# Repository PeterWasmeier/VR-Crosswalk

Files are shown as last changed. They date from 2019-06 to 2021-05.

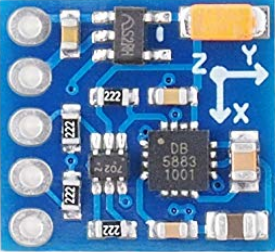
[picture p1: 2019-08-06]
Mini/Documents/Triple Axis Compass - GY271/GY271.png

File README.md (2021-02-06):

# VR-Crosswalk
Documents, Source code, wiring and 3D files of the omnidirectional treadmill "VR-Crosswalk"

About the subfolders:

- "Introduction"
Contains documents, describing the "VR-Treadmill" in general. If you don't know what it this repository about, first read the documents inside this folder.

- "Algorithms"
There you will find some documents, describing the math behind this treadmill.

- "Mini"
This "Mini" version is just a proof of concept, it's not suitable for humans, can't take weights and is just for your desk to play with. 

- "Light"
The "Light" version is a real omnidirectional treadmill for humans, but not able to handle stairs and elevators. Walking, sitting and driving a car is possible.

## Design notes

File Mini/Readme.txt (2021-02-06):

In this folder, there are all 3D files, wiring and source code of the "VR-Crosswalk-Mini".

This "Mini" version is just a proof of concept, it's not suitable for humans, can't take weights and is just for your desk to play with. 

The "Mini" version is also not able to handle stairs, elevator or cars, just: testing the formulars and a proof of concept. Maximum shoe length is 160mm or "22" (EU shoe size).

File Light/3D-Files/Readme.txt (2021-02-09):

This folder contains 3D files for the "VR-Crosswalk-Light". These files are created with "Autodesk Fusion 360".

Here are two subfolders:

- "general"
Here you will find 3D files of items that you can buy on Amazon, Ebay, and so on. These parts are needed by the "VR-Crosswalk-Light".

- "special"
The 3D parts inside this folder are special for the "VR-Crosswalk-Light". You can't buy them, you have to create them by your own.

- "Fusion360"
This is a backup what is currently in development. This is the whole machine with all parts and screws. Will be updated around once a week.

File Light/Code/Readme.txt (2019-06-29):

The source-code is made for the hardware: "Arduino Uno".

You have to use the IDE "Arduino Genuino V1.8.9" in order to open this project. 

You can download the IDE here:

http://www.arduino.cc/

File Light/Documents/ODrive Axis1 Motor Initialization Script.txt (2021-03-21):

odrv0.axis1.motor.config.pole_pairs=7
odrv0.axis1.controller.config.input_mode=INPUT_MODE_TRAP_TRAJ
odrv0.axis1.motor.config.motor_type = MOTOR_TYPE_HIGH_CURRENT
odrv0.axis1.motor.config.current_lim=25
odrv0.axis1.controller.config.vel_limit=20
odrv0.axis1.motor.config.calibration_current=2
odrv0.axis1.motor.config.torque_constant=0.0147678571428571
odrv0.axis1.motor.config.pre_calibrated = False
odrv0.axis1.encoder.config.use_index=False
odrv0.axis1.encoder.config.pre_calibrated=False
odrv0.save_configuration()
odrv0.reboot ()

odrv0.axis1.encoder.config.bandwidth = 3000
odrv0.axis1.encoder.config.mode = ENCODER_MODE_INCREMENTAL
odrv0.axis1.encoder.config.cpr=8192
odrv0.save_configuration()
odrv0.reboot ()

odrv0.axis1.requested_state = AXIS_STATE_FULL_CALIBRATION_SEQUENCE
dump_errors(odrv0)

odrv0.axis1.motor.config.pre_calibrated=True
odrv0.axis1.trap_traj.config.vel_limit = 0.5
odrv0.axis1.trap_traj.config.accel_limit = 140
odrv0.axis1.trap_traj.config.decel_limit = 140
odrv0.axis1.controller.config.inertia = 0
odrv0.axis1.controller.config.input_mode=INPUT_MODE_TRAP_TRAJ
odrv0.save_configuration()
odrv0.reboot ()

odrv0.axis1.encoder.config.use_index=True
odrv0.axis1.requested_state = AXIS_STATE_ENCODER_INDEX_SEARCH
odrv0.axis1.encoder.config.pre_calibrated=True
odrv0.save_configuration()
odrv0.axis1.encoder.is_ready
odrv0.reboot ()

odrv0.axis1.controller.config.pos_gain=56
odrv0.axis1.controller.config.vel_gain=0.053
odrv0.axis1.controller.config.vel_integrator_gain=0.05
odrv0.axis1.min_endstop.config.gpio_num=8
odrv0.axis1.min_endstop.config.debounce_ms=1
odrv0.axis1.min_endstop.config.is_active_high=True
odrv0.axis1.min_endstop.config.enabled=True
odrv0.save_configuration()
odrv0.reboot ()

odrv0.axis1.min_endstop.endstop_state
dump_errors(odrv0,True)

odrv0.axis1.requested_state = AXIS_STATE_ENCODER_INDEX_SEARCH
odrv0.axis1.encoder.is_ready
dump_errors(odrv0,True)

odrv0.axis1.requested_state = AXIS_STATE_CLOSED_LOOP_CONTROL
odrv0.axis1.controller.input_pos=
odrv0.axis1.requested_state = AXIS_STATE_IDLE

odrv0.axis1.controller.config.vel_ramp_rate=0.5
odrv0.axis1.min_endstop.config.offset=2
odrv0.axis1.controller.config.homing_speed=-0.5
odrv0.axis1.requested_state=AXIS_STATE_HOMING

AXIS_ERROR_HOMING_WITOUT_ENDSTOP
**********************************************************
Tuning

odrv0.axis1.controller.config.pos_gain=20
odrv0.axis1.controller.config.vel_gain=0.04
odrv0.axis1.controller.config.vel_integrator_gain=0

odrv0.axis1.requested_state = AXIS_STATE_CLOSED_LOOP_CONTROL
odrv0.axis1.controller.input_pos=
odrv0.axis1.requested_state = AXIS_STATE_IDLE
dump_errors(odrv0,True)

odrv0.axis1.requested_state = AXIS_STATE_ENCODER_INDEX_SEARCH
odrv0.axis1.encoder.is_ready
dump_errors(odrv0,True)

start_liveplotter(lambda:[odrv0.axis1.encoder.pos_estimate, odrv0.axis1.controller.pos_setpoint])

start_liveplotter(lambda:[odrv0.axis1.motor.current_control.Iq_setpoint,odrv0.axis1.motor.current_control.Iq_measured])

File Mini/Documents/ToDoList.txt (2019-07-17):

Some Notes from Peter Wasmeier for stuff to improve

- den Arduino anders herum platzieren (180° gedreht) da sonst der USB Anschluß nicht genutzt werden kann (Motor im Weg!)
* die 4er Löcher in den unteren Trittplatten müssen 0,1mm größer werden
-die 3mm Löcher in der Platine müssen auch wirklich 3mm haben sonst lässt sich die Platine nicht mit der PCB Grundplatte verschrauben
*es muss ein Kabelloch für den Encoder rein
-die PCB Platte doch mit 4mm dicke? Weil es wakelt zu viel, oder aber eine Unterlegscheibe unter den SK8. Vorher aber prüfen ob die Lötpunkte unter der Trittplattenplatine ausreichend sind um den Millimeter zu überbrücken zwischen Alu-Trittplatte und Base.
*die 5er Schraubenlöcher der SK Teile kleiner, damit dort ein Gewinde rein kann
*das Loch für die Stepper um 0,1mm größer machen
- prüfen ob der kleine Servo mehr als nur 180° beherrscht, sonst lassen sich die Beine nicht kreuzen
- die Formeln der Platte auf vier Quadranten verteilen

Legende:
- noch zu tun
* bereits erledigt

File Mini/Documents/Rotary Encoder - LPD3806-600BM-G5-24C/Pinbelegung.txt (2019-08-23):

Die Belegung der Anschlüsse ist:
- sw(black) GND, 
- rt(red) VCC, 
- ws(white) PIN A, 
- gn(green) PIN B.
PIN A und PIN B sind Open Collector Ausgänge, also PullUp.Widerstände nicht vergessen zu programmieren.

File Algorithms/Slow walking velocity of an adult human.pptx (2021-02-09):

## Slow walking velocity of an adult human

The slow, normal walking speed of an adult human is around 3,5km/h.

α=atan((35cm)/(15cm))×180/π= 66,8°

Slow walking speed | 3,5km/h
Step length at 3,5km/h around | 70cm
Steps per hour (with 70cm) | 5000
Time to take a single step (70cm) | 0,72s
Feet distance while standing | 30cm

In other words
To take one full step (70cm) in 0,72s, the axis
has to rotate from 0° to +66,8°.
This makes around 92,8° per second or 15,5rpm
where the disc has to spin.

Note: 15,5rpm is not the fastest speed which has to be
achieved, because the rotation speed depends on
tangens and the feet distance (while standing).

70cm

35

α

-20

-10

10

20

-35

30cm

## Walking straight ahead with 70cm in 0,72s

Note: as you can see, the highest rpm is about 30rpm or 180°/second.

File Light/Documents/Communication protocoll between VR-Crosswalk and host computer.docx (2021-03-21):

# VR-Crosswalk

## Communication protocol between VR-Crosswalk and host computer.

The device VR-Crosswalk can tell the host computer where the foots of the operator are located, in which angle each foot is currently orientated and the current state of the device.

The communication between VR-Crosswalk and the host computer is using Bluetooth. The communication speed is 38400 baud, 8 data bits. There is no need to select stop-bit or parity, it doesn’t matter. The host must look for the Bluetooth device “VR-Crosswalk”, connect to it and the Bluetooth connection can be handled as a normal COM port (RS232). The PIN, to connect to the device, is by default: 1234

Once the connection is established, and the host is listening on the COM port, the device will send its current state, each foot location and orientation by itself as soon as a foot has moved.

The host computer can also ask the device to move any axis. But in this case, it is forbitten for the operator to use the device. If host send a move command, but an operator is detected by the device, the command is rejected. For safety reason, each axis movement will be performed in very slow speed.

The communication between host and VR-Crosswalk is done by using 6 bytes data packages. Every data package is 6 bytes long. There are up to looks like this:

1.Byte | 2.Byte | 3.Byte | 4.Byte | 5.Byte | 6.Byte
Message ID | Value #1 (8 Bits) | Value #2 (8 Bits) | Value #3 (8 Bits) | Value #4 (8 Bits) | Checksum
Message ID | Value #1 (16 Bits, signed INT) | | Value #2 (16 Bits, signed int) | | Checksum
Message ID | Value #1 (32 Bits, signed long) | | | | Checksum
Message ID | Value #1 (32 bits as float) | | | | Checksum

The checksum is an XOR operation of the first five bytes.

Commands from host to VR-Crosswalk

Rotate device

This command, send by host, will rotate the VR-Crosswalk by the given value in units. This movement is relative. So, if you want to rotate the device by 200 units from the current position, set for Value #1 the number 200.

1.Byte | 2.Byte | 3.Byte | 4.Byte | 5.Byte | 6.Byte
Message ID | Value #1 (32 Bits as signed long) | | | | Checksum
0x10 | any positive or negative number | | | | Checksum

### Current state

The current state is sent from VR-Crosswalk to the host computer every 0,1 seconds. The state is four bytes long. Its value is defined as:

Byte | 1 | | | | | | | | 2 | | | | | | | | 3 | | | | | | | | 4
Bit | 7 | 6 | 5 | 4 | 3 | 2 | 1 | 0 | 7 | 6 | 5 | 4 | 3 | 2 | 1 | 0 | 7 | 6 | 5 | 4 | 3 | 2 | 1 | 0 | CRC
| 0 | 0 | 0 | 0 | 0 | 0 | 0 | 0

- Byte 2, Bit 7:

### Left Foot location, X-Coordinate

Byte | 1 | | | | | | | | 2 | 3 | 4
Bit | 7 | 6 | 5 | 4 | 3 | 2 | 1 | 0 | Lowbyte | Highbyte | CRC
| 0 | 0 | 0 | 0 | 0 | 0 | 0 | 1 | X-Coordinate in 0,1mm | X-Coordinate in 0,1mm

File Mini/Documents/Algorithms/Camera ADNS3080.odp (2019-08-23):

## Virtual Reality Treadmill "Crosswalk"

## Thema: Trittplatten die den Füßen folgen

## Virtual Reality Treadmill "Crosswalk"

## Vorwort

In diesem Dokument geht es darum, wie das Gerät den Füßen des Menschen folgen kann.

Hierfür werden Sensoren und Aktoren benötigt und die notwendigen Formeln hergeleitet.

## Aufbau von “Crosswalk”

## die Plattform kann sich um sich selbst drehen

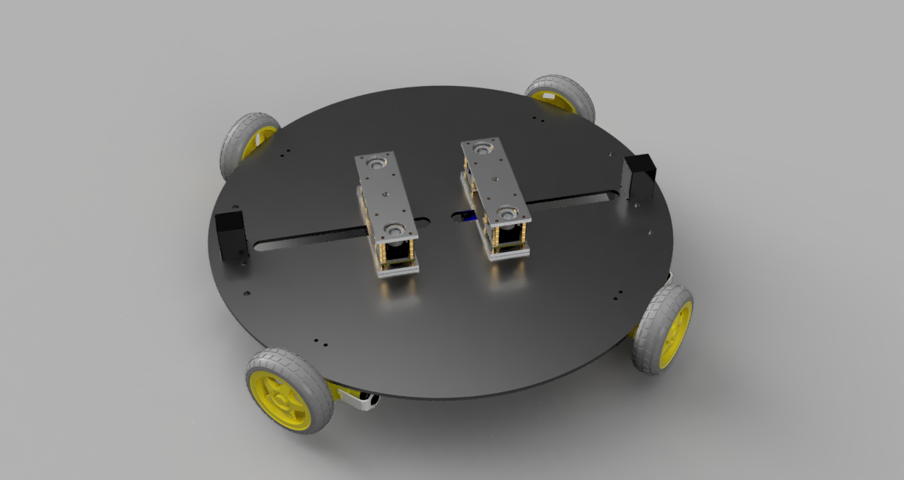
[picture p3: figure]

1. Trittplatte

2. Trittplatte

d

2 Motoren für

die horizontale

Ausrichtung

der Trittplatten.

Plattform

4 Motoren

## die horizontale Achse Ansicht von unten

## die Trittplatten sind mit einem Zahnriemen verbunden

Drehen sich diese Motoren,
ändert sich der Abstand der
Trittplatten.

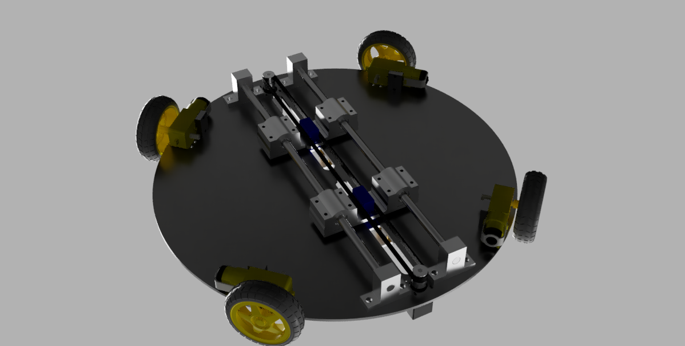
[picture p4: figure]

d

## eine Trittplatte für jeden Fuß

## auf einer Trittplatten sind Sensoren anzuordnen

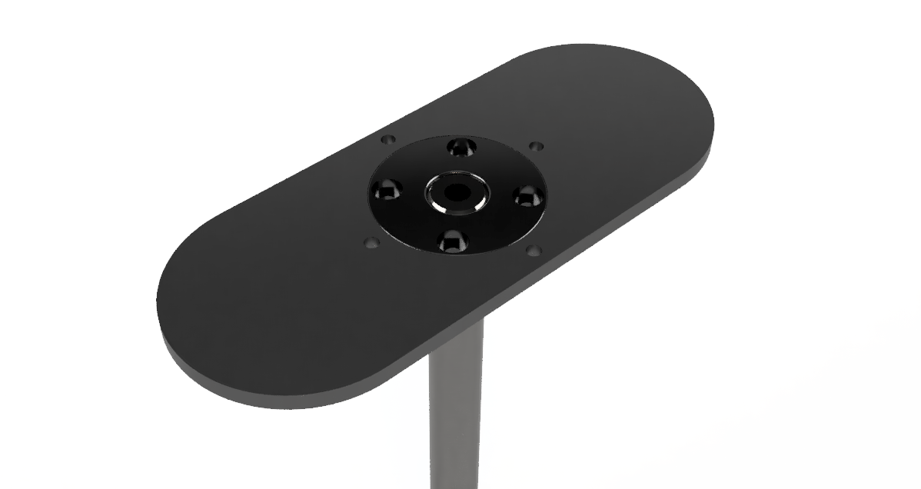
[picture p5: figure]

## geeignete Sensoren

## ADNS3080

Bei dem ADNS3080 handelt es sich um einen

Sensor wie er in vielen Computermäusen

eingebaut ist.

Dieser erfasst die X- und Y- Bewegungsrichtung

gegenüber einer Oberfläche.

Wenn dieser Sensor auf der Trittplatte befestigt wird, wird er die Bewegungsrichtung des Fußes gegenüber der stillstehenden Trittplatte erfassen.

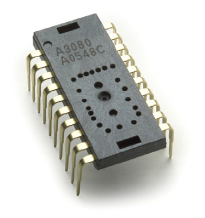
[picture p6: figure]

## geeignete Sensoren

## ADNS3080

Diesen Sensor gibt es

auch mit einer Linse.

Diese Linse ermöglicht es dem Sensor

zusätzlich in die Tiefe zu “sehen”.

Mit 15,-€ ist dieser Sensor recht günstig.

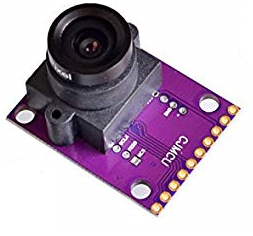
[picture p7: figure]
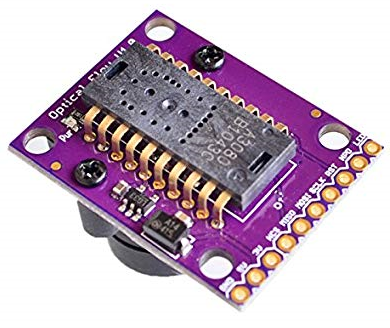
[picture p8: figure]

## Positionierung der Sensoren

## die Trittplatte kann sich drehen

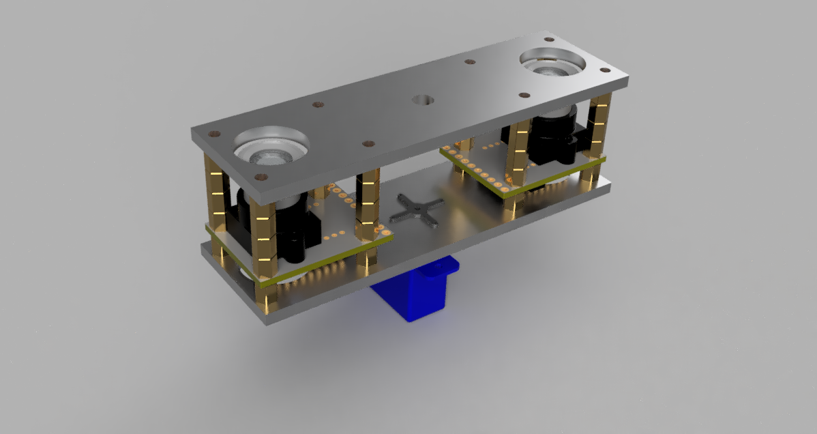
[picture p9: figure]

erster ADNS3080

Trittplatte

zweiter ADNS3080

Hinweis:
die Sensoren sind um 180°

gegeneinander verdreht.

Servo:

dreht die Trittplatte

## Mögliche Fußbewegungen

## vor/zurück, links/rechts und um sich selbst drehen

d

## ∆x und ∆y Daten vom ADNS3080

## beide ADNS3080 liefern delta-Werte

Jeder Sensor liefert

delta-Werte für

x und y sobald eine

Bewegung erkannt

wird.

Wichtig: die delta-
Werte sind senkrecht
zum Sensor.

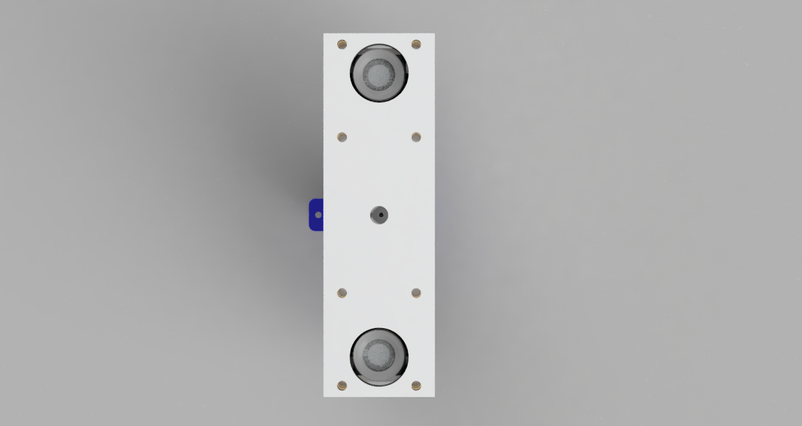
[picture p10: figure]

∆x₁

∆y₁

Bei m handelt es sich

um den konstanten
Abstand der Sensoren.

∆y₂ und ∆x₂ sind deshalb
negativ, da die Kamera
auf dem Kopf steht.

m

-∆y₂

-∆x₂

## ein Fuß wird bewegt 1. neue Position im Raum

## die Koordinaten von x₁ / y₁ und x₂ / y₂ ändern sich

∆x₁

∆y₁

-∆x₂

-∆y₂

(x₂ / y₂)

(x₁ / y₁)

(x'₁ / y'₁)

(x'₂ / y'₂)

x'₁=x₁+∆x₁

y'₁=y₁+∆y₁

x'₂=x₂-∆x₂

y'₂=y₂-∆y₂

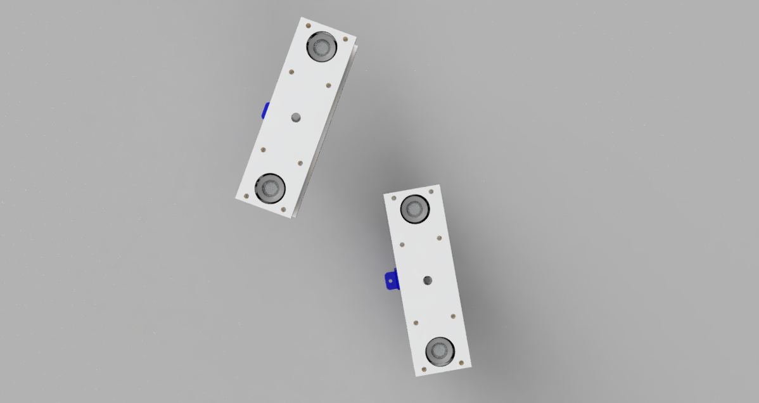
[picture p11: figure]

ursprüngliche
Position des Fußes

neue Position
des Fußes im Raum

## ein Fuß wird bewegt 2. Mitte der Trittplatte

## die Mitte wird später horizontal bewegt

(x'₁ / y'₁)

(x'₂ / y'₂)

(fx / fy)

fx={x'₁+x'₂} over {2}

fy={y'₁+y'₂} over {2}

Mitte der Trittplatte

## ein Fuß wird bewegt 3.Abstand der Trittplatte zum Zentrum

## der Abstand b zum Drehzentrum ist zu berechnen

(x'₁ / y'₁)

(x'₂ / y'₂)

(fx / fy)

b

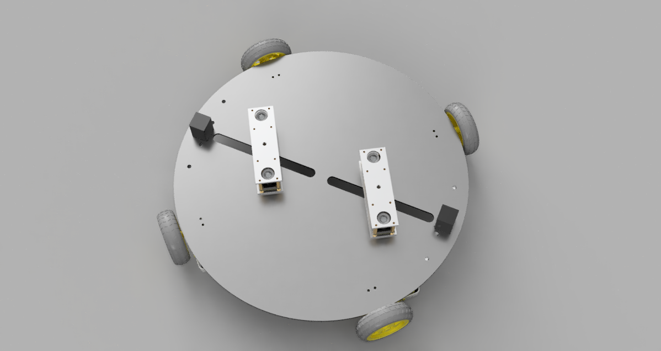
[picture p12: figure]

Zentrum

d

## ein Fuß wird bewegt 3.Abstand der Trittplatte zum Zentrum

## die Entfernung b ist zu berechnen

(x'₁ / y'₁)

(x'₂ / y'₂)

Zentrum

(0 / 0)

(fx / fy)

b

b=nroot{2}{fx²+fy²}

fy

fx

## ein Fuß wird bewegt 4.Winkel der Plattform

## die Plattform muss den Winkel α einnehmen

(x'₁ / y'₁)

Zentrum

(x'₂ / y'₂)

b

(0 / 0)

(fx / fy)

α=arcsin({fy} over {b} )

fy

α

fx

## Meßfehler der Sensoren erkennen 5. Abstand der Sensoren

## der Abstand m und m' stimmen nicht mehr überein

∆x₁

∆y₁

-∆x₂

-∆y₂

(x₂ / y₂)

(x₁ / y₁)

(x'₂ / y'₂)

(x'₁ / y'₁)
Der obere ADNS3080
sollte sich laut Formel
eigentlich hier befinden.

m

m'

Ursprüngliche
Position des Fußes

Neue Position
des Fußes

Wenn ein Messfehler auftritt,
verändert sich der Abstand
der zwei Sensoren.

## Meßfehler der Sensoren erkennen 5. Abstand der Sensoren

## m' ist mit dem tatsächlichen Abstand m zu vergleichen

(x'₁ / y'₁)

(x'₂ / y'₂)

m'

∆x'₁₂ = x'₁ - x'₂

∆y'₁₂ = y'₁ - y'₂

m'=nroot{2}{(∆x'₁₂)²+(∆y'₁₂)²}

if m' NOT m then ERROR

∆y'₁₂

∆x'₁₂

## ein Fuß wird bewegt 6. Rotation der Trittplatte

## der Winkel β der Rotation ist zu berechnen

(x'₁ / y'₁)

(x'₂ / y'₂)

β=arcsin({x'1-x'2} over {m'})

β

## Zusammenfassung der Formeln

x'₁=x₁+∆x₁

y'₁=y₁+∆y₁

x'₂=x₂-∆x₂

y'₂=y₂-∆y₂

1. neue Position
im Raum

fx={x'₁+x'₂} over {2}

fy={y'₁+y'₂} over {2}

2. Mitte der Trittplatte

b=nroot{2}{fx²+fy²}

3. Abstand der Trittplatte zum Zentrum

∆x'₁₂ = x'₁ - x'₂

∆y'₁₂ = y'₁ - y'₂

m'=nroot{2}{(∆x'₁₂)²+(∆y'₁₂)²}

5. Abstand

Sensoren

α=arcsin({fy} over {b} )

4. Winkel der Plattform

β=arcsin({x'1-x'2} over {m'})

6. Rotation der Trittplatte

## Zusammenfassung Werte

## von den Formeln zurück gelieferte Werte

Beide Trittplatten liefern je ein ...

- b Hierbei handelt es sich um den Abstand einer Trittplatte zum Zentrum
- α der Winkel der Plattform
- β den Winkel den die Trittplattform einnehmen muss

## Fragen

## von den Formeln zurück gelieferte Werte

Zu entscheiden ist nunmehr:

a) welche Trittplatte ist dominant und bestimmt

die Werte für b, β und α?

b) welche Position hat die andere

Trittplatte einzunehmen?

## Antwort

## von den Formeln zurück gelieferte Werte

Die Werte von b, β und α werden von der Trittplatte herangezogen, dessen Fuß sich in der Luft befindet.

Die andere Trittplatte wird sich automatisch, sobald der Parameter α und b von der dominaten Trittplatte geändert wird, mechanisch verschoben und zieht dabei den auf der Trittplatte befindlichen Fuß automatisch mit sich.

Lediglich der Wert β für die nicht dominante Trittplatte muss angepasst werden.

## Der Wert β der nicht dominanten Trittplatte

## der linke Fuß wird angehoben und nach vorne bewegt

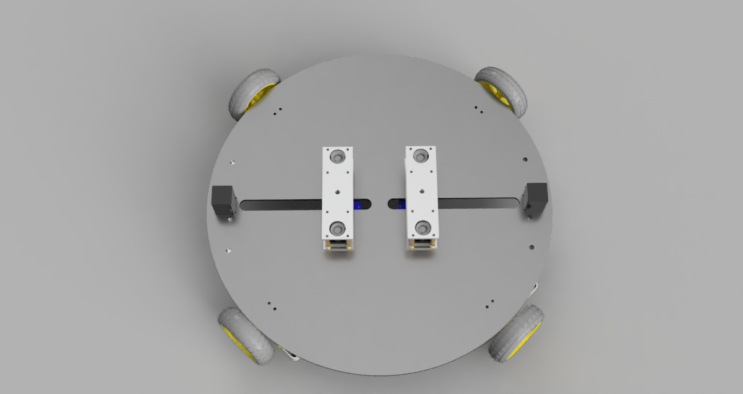
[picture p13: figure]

der linke Fuß wird
nach vorne bewegt

## die Plattform dreht sich, die linke Trittplatform ist Ok, rechts fehlerhaft

## die rechte Trittplattform muss sich anpassen

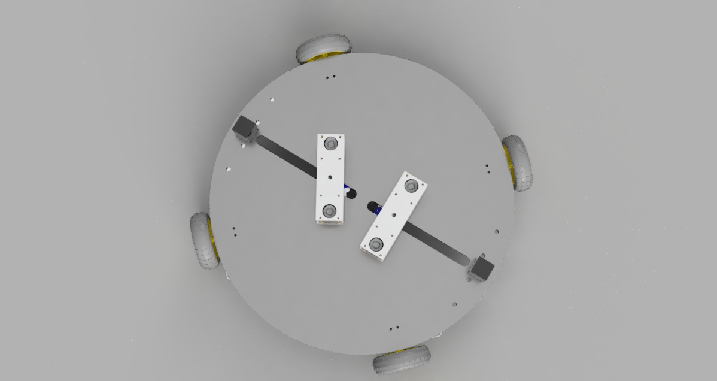
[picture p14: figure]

falsche Ausrichtung

## korrekte Position beider Trittplatten

## die rechte Trittplattform dreht sich “mit”

∆β = -∆α

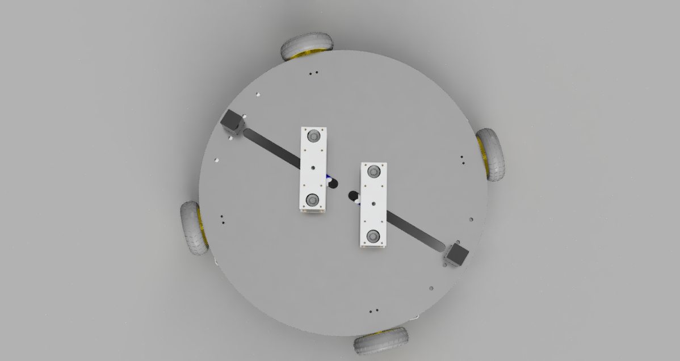
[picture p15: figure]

korrekte Ausrichtung

## korrekte Position der nicht dominanten Trittplatte

## nun sind beide Trittplatten in Position

Verändert sich also α um ∆α, so hat sich das β der anderen Trittplatte um -∆α zu ändern.

Der Abstand b der nicht dominanten Trittplatte wird mechanisch durch den Zahnriemen um den selben Betrag geändert.

## Schlußbemerkung

In diesem Dokument wird nicht darauf eingegangen, wie erkannt werden soll ob sich ein Fuß auf einer Trittplatte befindet oder nicht, bzw. welche der beiden Trittplatten dominant ist.

Was hier auch nicht erwähnt wurde, sind die Werte für ∆x₁ ∆y₁ ∆x₂ ∆y₂ sobald sich der Fuß von dem Sensor ADNS3080 entfernt.

Denn in diesem Fall sind die Werte für ∆x₁ ∆y₁ ∆x₂ ∆y₂ mit der Höhe des Fußes zu verrechnen.

Andernfalls sind die Werte für ∆x₁ ∆y₁ ∆x₂ ∆y₂ nicht korrekt.

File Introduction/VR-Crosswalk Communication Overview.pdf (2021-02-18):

# VR-Crosswalk

COMMUNICATION BETWEEN EACH COMPONENT

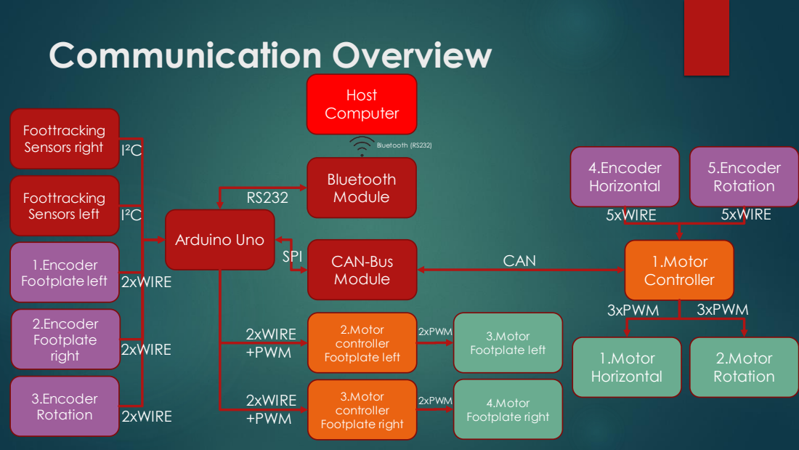
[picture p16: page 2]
Communication Overview; Arduino Uno; Bluetooth Module; CAN-Bus Module; 1.Motor Controller; 2.Motor Rotation; 1.Motor Horizontal; Host Computer; 2.Motor controller Footplate left; 3.Motor controller Footplate right; 4.Encoder Horizontal; 5.Encoder Rotation; 1.Encoder Footplate left; 2.Encoder Footplate right; 3.Encoder Rotation; 3.Motor Footplate left; 4.Motor Footplate right; Foottracking Sensors left; Foottracking Sensors right; SPI; 2xWIRE +PWM; I²C; CAN; 2xWIRE; 5xWIRE; 2xPWM; 3xPWM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

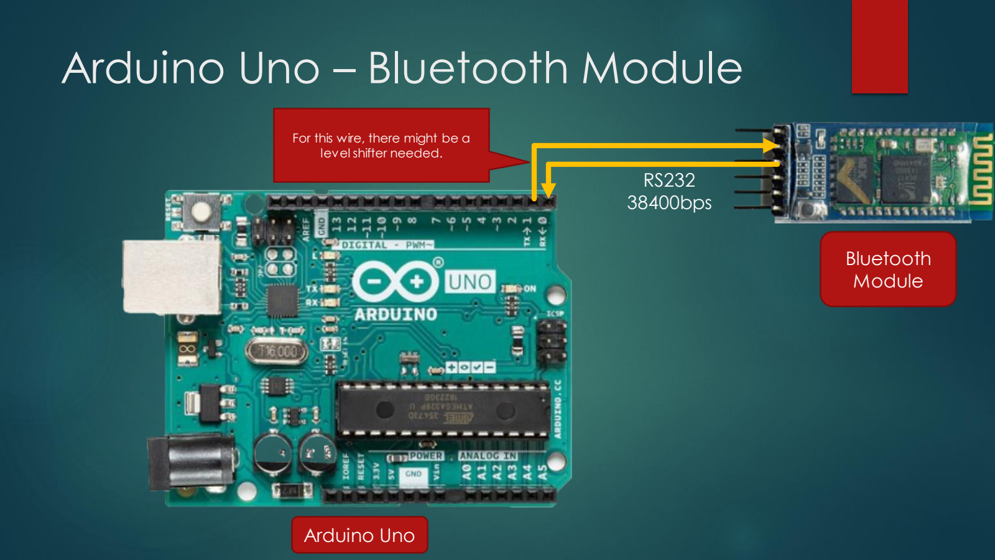
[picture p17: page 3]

Arduino Uno – Bluetooth Module

Arduino Uno

RS232
38400bps

Bluetooth
Module

For this wire, there might be a level shifter needed.

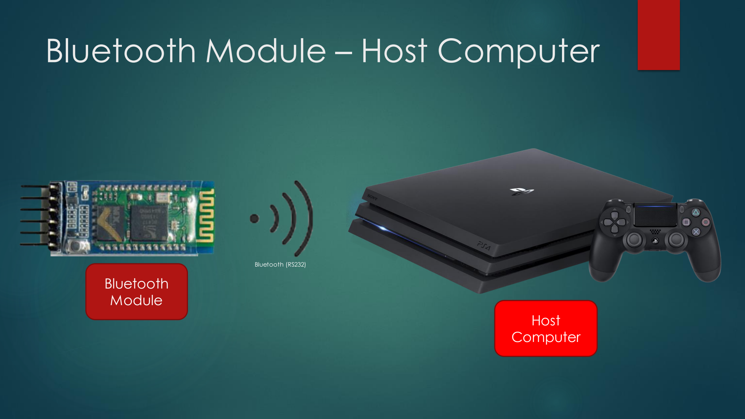
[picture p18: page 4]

Bluetooth Module – Host Computer

Bluetooth
Module
Host
Computer

Bluetooth (RS232)

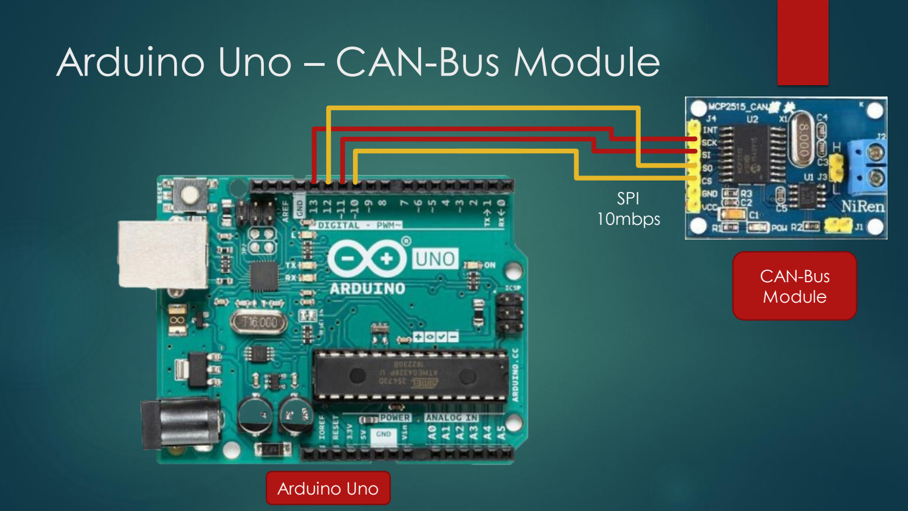
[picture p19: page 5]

Arduino Uno – CAN-Bus Module

Arduino Uno

CAN-Bus
Module

SPI
10mbps

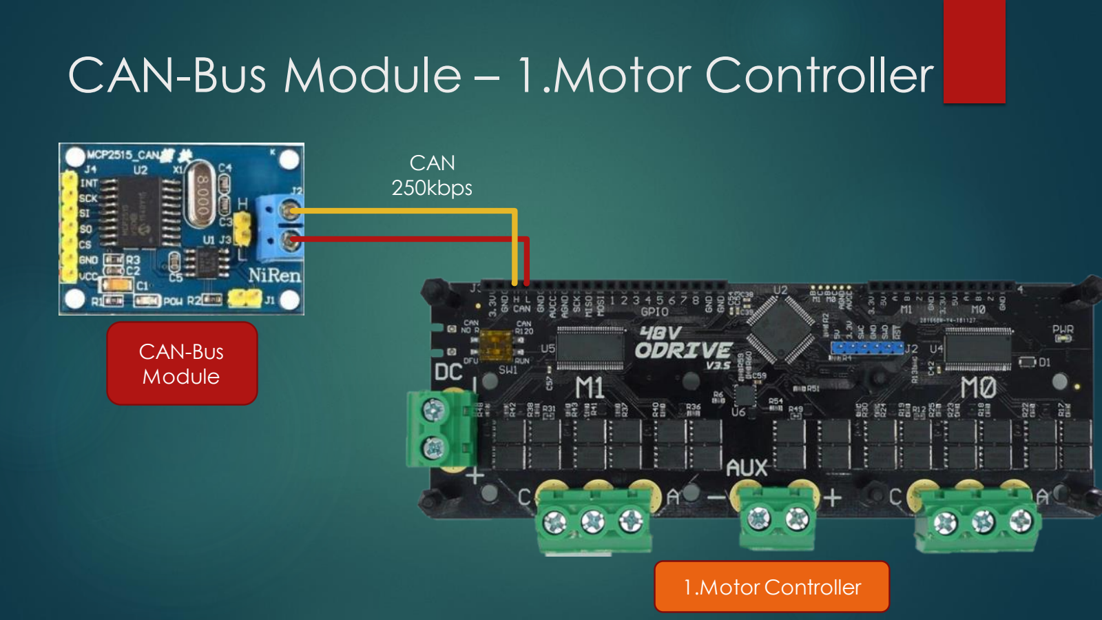
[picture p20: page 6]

CAN-Bus Module – 1.Motor Controller

CAN-Bus
Module

1.Motor Controller

CAN
250kbps

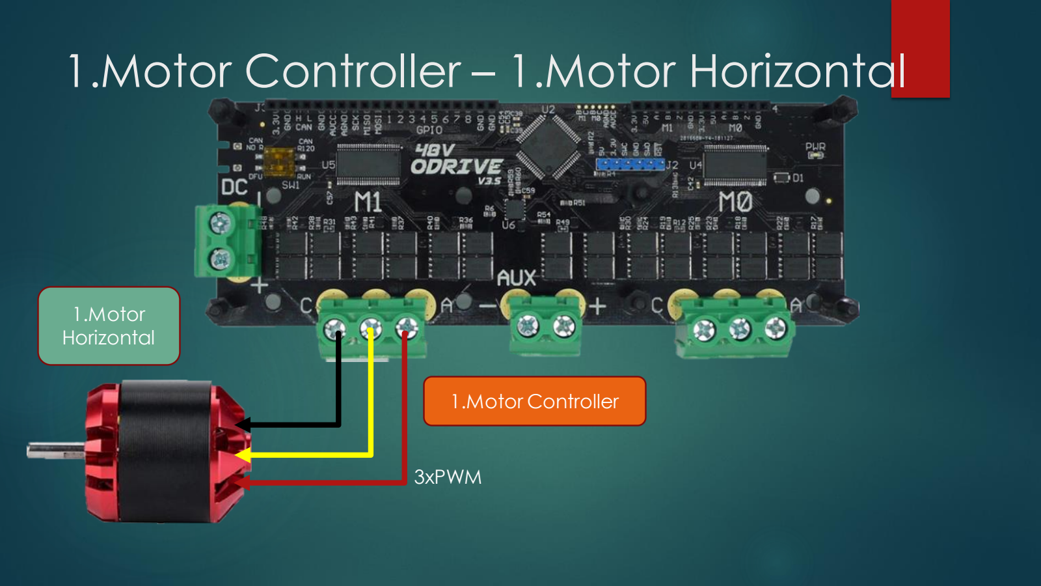
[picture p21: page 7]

1.Motor Controller – 1.Motor Horizontal

1.Motor Controller

1.Motor
Horizontal

3xPWM

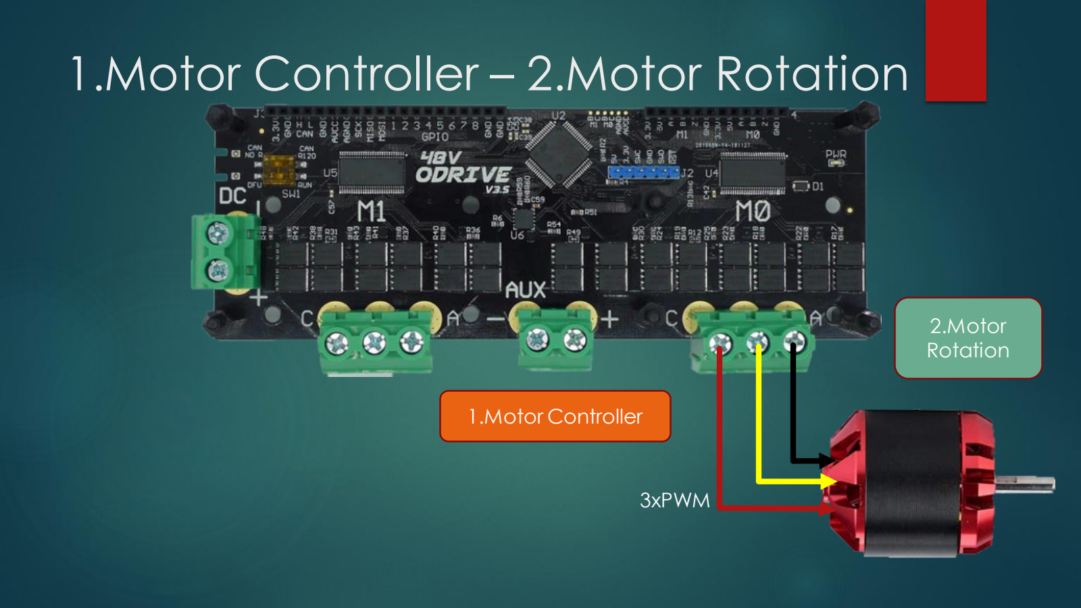
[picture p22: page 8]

1.Motor Controller – 2.Motor Rotation

1.Motor Controller

2.Motor
Rotation

3xPWM

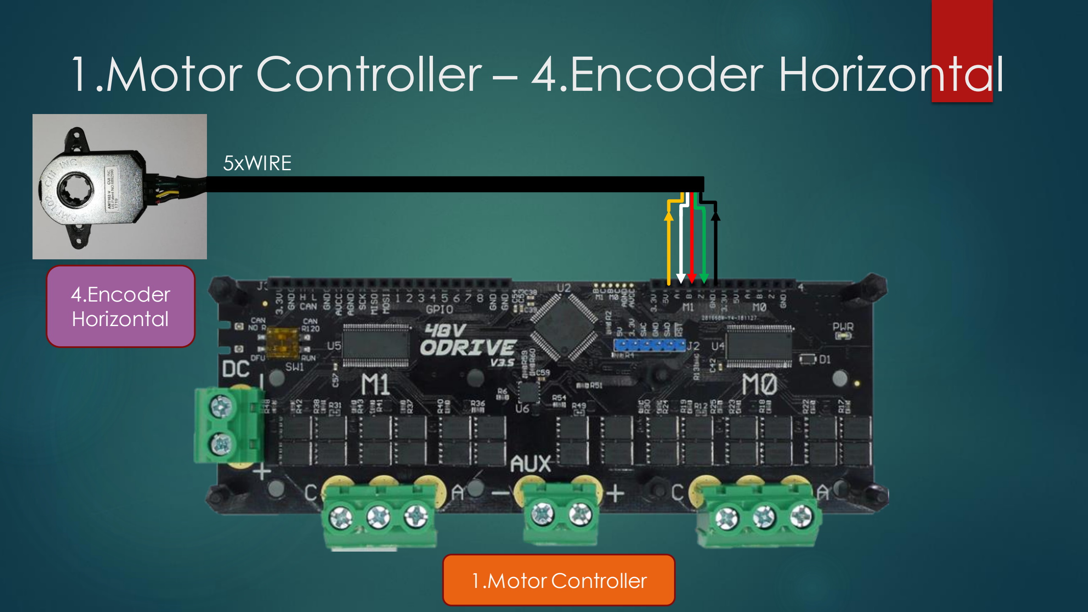
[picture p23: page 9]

1.Motor Controller – 4.Encoder Horizontal

1.Motor Controller

4.Encoder
Horizontal

5xWIRE

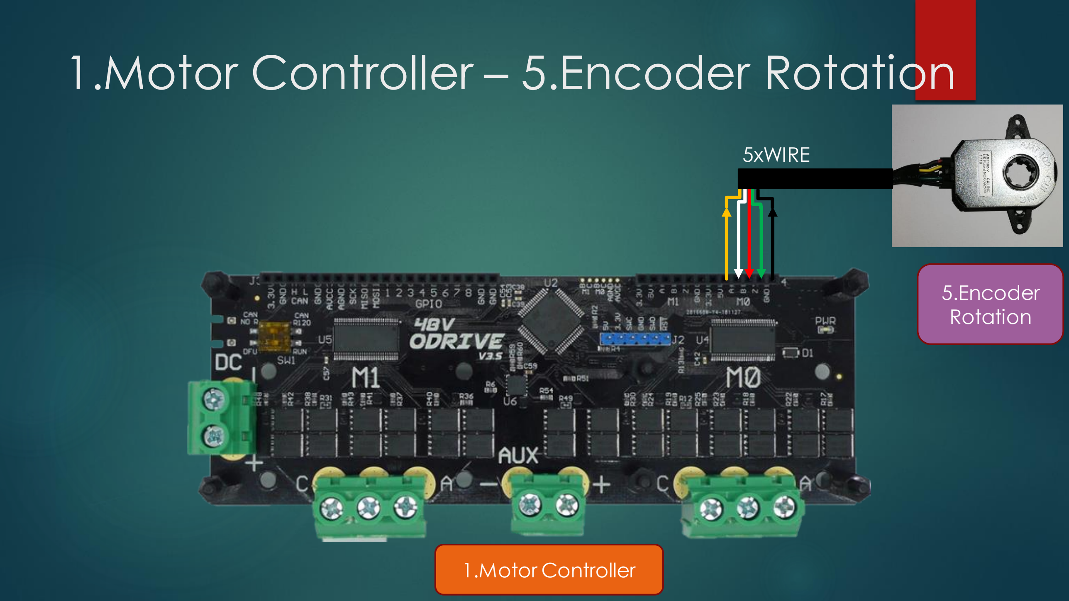
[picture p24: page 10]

1.Motor Controller – 5.Encoder Rotation

1.Motor Controller

5.Encoder
Rotation

5xWIRE

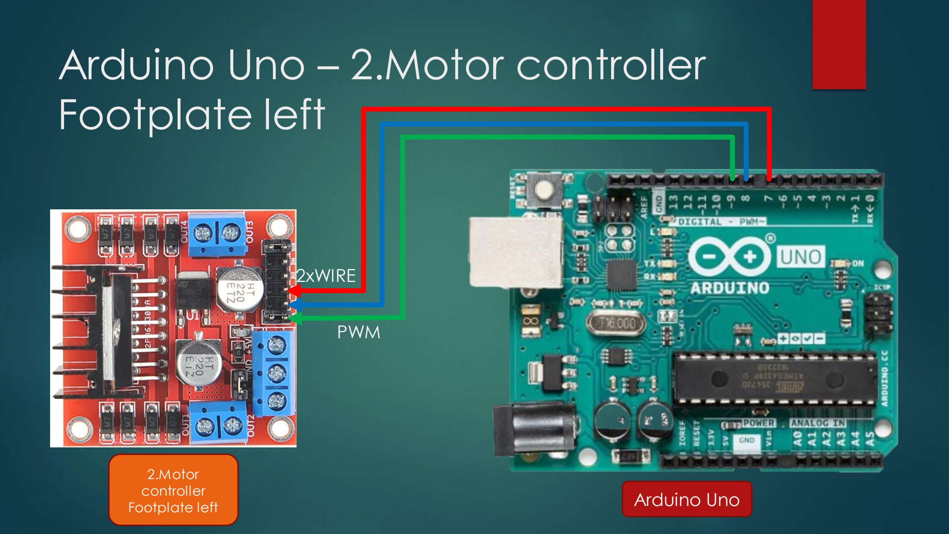
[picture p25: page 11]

Arduino Uno – 2.Motor controller Footplate left

Arduino Uno

2.Motor
controller
Footplate left

PWM

2xWIRE

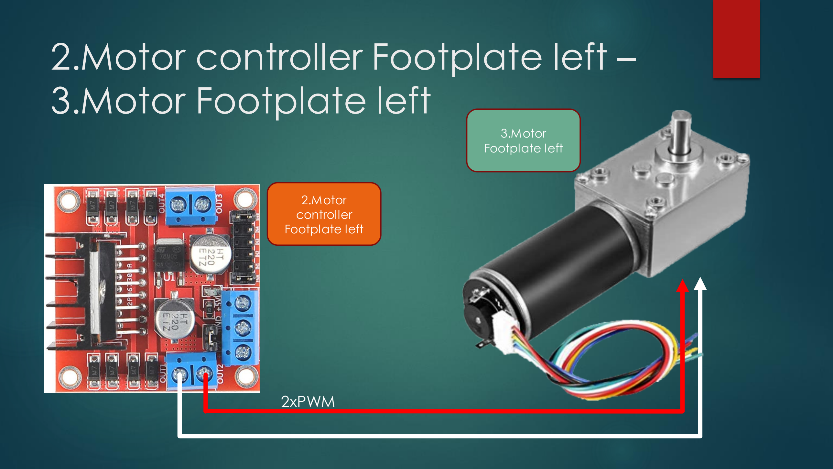
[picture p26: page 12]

2.Motor controller Footplate left – 3.Motor Footplate left

2.Motor
controller
Footplate left

2xPWM

3.Motor
Footplate left


Arduino Uno – 1.Encoder Footplate left

Arduino Uno

2xWIRE

1.Encoder
Footplate left


Arduino Uno – 3.Motor controller Footplate right

Arduino Uno

PWM

3.Motor
controller
Footplate right

2xWIRE


3.Motor controller Footplate right – 4.Motor Footplate right

3.Motor
controller
Footplate right

2xPWM

4.Motor
Footplate right


Arduino Uno – 2.Encoder Footplate right

Arduino Uno

2xWIRE

2.Encoder
Footplate
right


Arduino Uno – 3.Encoder Rotation

Arduino Uno

2xWIRE

3.Encoder
Rotation


Arduino Uno – Foottracking Sensors left

Arduino Uno

I²C
400kbps

Foottracking
Sensors left


Arduino Uno – Foottracking Sensors right

Arduino Uno

I²C
400kbps

Foottracking
Sensors right


Arduino Uno – PIN Overview

--- CAN-Bus Module (S0)

--- CAN-Bus Module (SCK)

--- CAN-Bus Module (SI)

--- CAN-Bus Module (CS)

--- 2.Motor controller Footplate left (PWM/Enable)

--- 2.Motor controller Footplate left (EN1)

--- 2.Motor controller Footplate left (EN2)

--- 3.Motor controller Footplate right (PWM/Enable)

3.Motor controller Footplate right (EN1) ---

3.Motor controller Footplate right (EN2) --- | --- 3.Encoder Rotation (Channel B) --- 3.Encoder Rotation (Channel A)

--- Bluetooth Module (RX)

--- Bluetooth Module (TX)

Foottracking Sensors (SDA) ---

Foottracking Sensors (SCL) ---

--- 2.Encoder Footplate right (Channel A)

--- 2.Encoder Footplate right (Channel B)

1.Encoder Footplate left (Channel A) ---

1.Encoder Footplate left (Channel B) ---

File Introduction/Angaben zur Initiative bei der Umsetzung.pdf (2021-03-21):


# EIGENE DARSTELLUNG DER ERFINDUNG

## EXPOSEE

### Angaben zur Initiative bei der Umsetzung

## Wasmeier, Peter

### Bedienvorrichtung, um sich in der

virtuellen | Realität | gattungsgemäß
fortbewegen zu können.

## ANGABEN ZUR INITIATIVE BEI DER UMSETZUNG

### Vorgehensweise bei der Erfindung

Inspiriert durch den Film „Ready Player One“, wollte ich VR selbst einmal ausprobieren. Einige Monate habe ich damit zugebracht, mir eine Vorrichtung zu überlegen die das Gehen in VR möglichst authentisch simulieren kann. Anschließend wurden die gewünschten Abmessungen der Vorrichtung, in Abhängigkeit der größten zu erwartender Schrittweite und Schuhgrößen ermittelt, damit das Gerät auch in einer kleinen Wohnung Platz findet. Somit standen dann die Länge und Breite der Trittplatten als auch der Durchmesser der Vorrichtung selbst fest. Bezüglich der Höhe des Gerätes ist es mir wichtig, dass man es gut verstauen kann. Dazu wurde eine Variante der Vorrichtung mit einer maximalen Höhe von 10cm festgelegt, so dass es auch unter einem Möbelstück Platz findet. Beispielsweise unter einem Bett oder ggf. auch unter einem Wohnzimmertisch. Diese Variante der Vorrichtung wird es jedoch nicht ermöglichen Treppen zu steigen. Zusätzlich wurde festgelegt, dass jede Variante der Vorrichtung einen Benutzer von 100kg tragen muss.

Mit diesen gesetzten Vorgaben wurden die ersten 3D-Zeichnungen angefertigt. Anschließend wurde nach Komponenten gesucht wie: Motoren, Linearachsen, etc., die in der Vorrichtung Platz finden. Mittels einer Software zur Simulation von Kräften wurde ermittelt ob die Vorrichtung einem Benutzer mit 100kg tragen kann. Bei der Suche nach Komponenten und Lieferanten habe ich konsequent auf den Preis geachtet/bzw. angefragt, um später in der Summe der Einzelteile ein erschwingliches Gerät zur Verfügung zu stellen.

Der nächste Schritt war die Software-Entwicklung bzw. das Ermitteln der zur Steuerung notwendigen Formeln. Hierzu habe ich ein Modell meiner Vorrichtung entwickelt und anschließend gebaut. Mit Hilfe dieses Modells konnte ich erstmals das Tracken der Füße und die Formeln mit echten Komponenten testen, statt nur zu simulieren.


Abbildung 1: 3D-Modell einer Testvorrichtung | Abbildung 2: Vorrichtung in Modellgröße

### Bewältigung von aufgetretenen Problemen

Es gibt zum jetzigen Zeitpunkt (06.JAN.2021) noch keinen fertigen Prototypen. Die Entwicklung und die Verbesserungen sind noch im vollen Gang. Dennoch gab und wird es weiterhin Probleme geben, die entweder schon aufgetreten sind oder aber schon behoben wurden. Dazu zählen unter anderem:

- Tracking der Schuhe
Mehrere Methoden zur Verfolgung der Schuhe wurden in Erwägung gezogen und einige von ihnen auch bereits am realen Modell getestet. Eine der Methoden ist vielversprechend. Welche Sensoren/Kameras später tatsächlich im fertigen Produkt eingesetzt werden, ist noch offen. Diese Vorrichtung kann jedoch auch die bereits verfügbaren HTC Vive Tracker nutzen, um beide Schuhe und die Vorrichtung selbst zu tracken. Sofern ich diese verwende, kann erheblich viel Zeit eingespart werden. Leider sind die HTC Vive Tracker sehr kostspielig.
- Gewicht
Von Anfang an habe ich auf das Gewicht der Vorrichtung geachtet. Um es möglichst niedrig zu halten, wurden leichte, aber belastbare Materialen verwendet. Ein geringes Gewicht erlaubt es dem Verbraucher die Vorrichtung auch kurzfristig zu transportieren. Beispielsweise unter dem Bett vorziehen, um dann im Schlafzimmer, einige Stunden VR erleben zu können. Ebenfalls sorgt ein leichtes Gewicht für höhere Beschleunigungen der Achsen, insbesondere der Rotationsachse, welche die Vorrichtung in Drehung versetzt. Dennoch wiegt die Vorrichtung bisher (08.02.2021) noch immer 33kg; noch nicht für alle Familienmitglieder geeignet.
- Unebener Fußboden/Standfläche
Damit die Vorrichtung auf vielen Oberflächen wie Parkett, Teppich, Fließen, etc. platziert werden kann, auch wenn diese etwas uneben oder rutschig sind, habe ich drei Gummi Standbeine für die Vorrichtung vorgesehen. Diese sorgen bei Unebenheit dafür, dass es nicht nur sicher steht, sondern auch wenig Vibrationen in den Fußboden übertragen werden. Dies ist für Mietswohnungen wichtig, da sich sonst der Nachbar darunter unter Umständen wegen der Lärmbelästigung beschwert. Mit einer Gummimatte können ggf. verbleibende Vibrationen zusätzlich reduziert werden.

### - Leistungsstarke Motoren und Motortreiber

Mehrere Motortreiber und Motoren sind noch im Test, um die Masse der Vorrichtung in Drehung versetzen zu können als auch die Trittplatten bzw. das Standbein ziehen oder schieben zu können. Industrielle Motoren und Motortreiber kommen aus Kostengründen nicht in Frage. Problematisch ist hier auch die Unterbringung der Motoren in das flache Gehäuse als auch das Finden von geeigneten Motoren mit der korrekten Achsenlänge, denn auf Sonderanfertigungen möchte ich soweit wie möglich verzichten.

- Designelemente
Damit die Vorrichtung auch optisch gut beim Verbraucher ankommt, plane ich neben einer LED-Beleuchtung, die rings herum angebracht wird, auch einen Stoffbezug rundherum, der sich „aufplustert“ sobald sich die Vorrichtung in Bewegung setzt und dabei in verschiedenen Farben schimmern kann.

### - Endverbraucherpreis

Der Gesamtpreis der Einzelteile muss möglichst gering sein, andernfalls wird es die Vorrichtung schwer haben sich am Markt für die Masse durchzusetzen. Dies versuche ich zu erreichen, indem ich fertig verfügbare Komponenten wähle, die es zu Massen auf dem Markt gibt. Beispielsweise Motoren und leistungsstarke Motortreiber, aus dem Hobby und Modellbau-Bereich. Nur wenige Teile sind aus dem Maschinenbaubereich, zum Beispiel die Linearachsen.

- Verschmutzung/Staub
Da damit zu rechnen ist, dass es im Inneren der Vorrichtung (durch die zwei Schlitze auf der Oberseite) zu Verunreinigungen kommt, sind diese durch Lamellen als auch durch einen Überdruck im Inneren zu schützen. Dieser Überdruck löst auch gleich das Problem mit der Abwärme der elektrischen Komponenten.
- Sicherheit
Es ist bei technischen Systemen immer mit Versagen zu rechnen. Aus diesem Grund ist es empfehlenswert diese Vorrichtung immer mit einer Art Bergsteigerausrüstung zu verwenden. Mit Hilfe eines Seiles, welches über der Vorrichtung befestigt wird, ist das Verletzungsrisiko geringer und löst bei Zug einen Not-Stopp aus. Damit sich die Plattform bei einem Notaus nicht drehen kann, sind Antriebe mit einer hohen Selbsthemmung zu verwenden. Beispielsweise Schneckengetriebe oder Spindeln. Ohne eine Selbsthemmung der Achsen verhält sich die Vorrichtung, sollte der Strom ausfallen, wie Glatteis, bzw. alle Achsen geben bei Belastung nach. Ebenfalls ist vorgesehen, dass sich die Vorrichtung sofort abschaltet, sollte das Gehäuse Hautkontakt registrieren. So können sich Kleinkinder nicht am Gerät verletzen, wenn ein Elternteil die Vorrichtung nutzt und dabei nicht bemerkt, dass sich der Nachwuchs nähert.
- Beschleunigungswerte
Die Rotationsachse, verantwortlich für die Drehung der Vorrichtung, als auch die horizontale Achse, für die Positionierung der Trittplatten, müssen hohe Beschleunigungswerte beim Aufsetzen eines Fußes erreichen. Nur so kann eine gleichbleibende Geschwindigkeit simuliert werden. Hierfür werden leistungsstarke Motoren eingesetzt (siehe technische Daten) als auch selbsthemmende Getriebe verwendet.
- Geräuschentwicklung
Damit die Immersion vollständig wird, sind nur Komponenten zu nutzen die einen sehr geringen Geräuschpegel entwickeln. Ich habe die Lautstärke der Vorrichtung noch nicht gemessen, konnte aber die kugelgelagerte Drehachse als auch die Linearachsen als lauteste Bauteile identifizieren. Die Linearlager werden in den kommenden Wochen durch Lineargleitbuchsen ersetzt. Für die kugelgelagerte Drehachse werde ich auch noch eine Lösung finden.

### bereits erfolgte oder geplante Verwertungsaktivitäten

Bisher sind keine Verwertungsaktivitäten erfolgt.

### mögliche Finanzierung

Bisher finanziere ich dieses Gerät mit meinen privaten Mitteln. Für die Zukunft plane ich eine Kickstarter Kampagne.

### Marktchancen

Soweit mir bekannt ist, ist diese Vorrichtung bislang die Erste ihrer Art. Ich sehe darin eine große Marktlücke, da noch keine geeigneten Geräte auf dem Markt sind, die eine solche hohe Immersion auf einer kleinen Fläche bieten. Diese Vorrichtung ist als Zubehör für VR-Brillen vorgesehen und richtet sich an VR-Nutzer. Sony, u.a. Anbieter einer VR-Brille, konnte bisher 5 Millionen VR-Headsets/Brillen verkaufen.

Quelle: https://mixed.de/playstation-vr-sony-hat-5-millionen-vr-brillen-verkauft/

Weitere Absatzmöglichkeiten sehe ich auch bei höherpreisigen VR-Brillen; beispielsweise bei der Vive-Index. Bei dieser Brille soll es sich um die meistverkaufte VR-Brille für den Personal Computer (PC) handeln.

Quelle: https://mixed.de/vr-brillen-verkaeufe-superdata-q4-2019/

### weitere Informationen

Zusammenarbeit mit Partnern
Bisher sind keine Partner vorhanden, ich bin aber offen für eine Zusammenarbeit.

Erweiterungen
Mit einer kleinen Modifikation wird es zusätzlich möglich sein einen PKW im Stehen zu betreten und diesen dann im Sitzen zu steuern oder sich auf eine Parkbank zu setzen. Ebenfalls ist es geplant auf dem Gerät zu tanzen, oder kleine Sprünge zur Seite zu tätigen. Mehr dazu in einem persönlichen Gespräch.

Technische Daten
Nachfolgend der Stand der Entwicklung vom 08.02.2021. Änderungen vorbehalten.
Gewicht: | 33kg
Maximale Schuhbreite: | 130mm (entspricht Schuhgröße 45)
Maximale Schuhlänge: | 330mm (entspricht Schuhgröße 45)
Durchmesser: | 982mm
Höhe: | 86.5mm
Geplante Belastbarkeit: | 100kg
Versorgungsspannung: | derzeit 12V, später 24V
Stromversorgung: | aktuell eine PKW-Batterie (12V), später zwei PKW-Batterien (24V) in Reihe
Leistung der Motoren: | zwei Motoren je 1.76KW, zwei weitere Motoren je ~24W
Altersempfehlung: | ab 16
Maximale Schrittlänge: | 732mm

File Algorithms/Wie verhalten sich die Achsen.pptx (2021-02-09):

## VR–Crosswalk: wie verhalten sich die Achsen?

Fragestellung:
Wie verhalten sich die zwei Achsen bei einer gleichbleibenden Geschwindigkeit?
Es ist davon auszugehen, dass sich die erste Achse wie ein „Tangens“ und die zweite Achse wie ein „Cosinus“ verhält.

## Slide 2

Bewegung

Hier sehen wir die runde Plattform mit zwei grünen Pfeilen. Die Pfeile stellen die Bewegungsrichtung der beiden Beine dar. Da die Pfeile senkrecht sind, handelt es sich also um einen Geradeauslauf. In diesem Beispiel soll das rechte Bein nach vorne, das linke nach hinten bewegt werden. Es handelt sich also um einen Schritt nach vorne, der mit dem rechten Bein durchgeführt wird.


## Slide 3

Achsen

Die Plattform kann sich um sich selbst (roter Pfeil, Winkel Alpha) und die Trittplatten nach links/rechts bewegen (violette Pfeile, Strecke L). Wichtig hierbei: die Strecke L wird von beiden Trittplatten zurück gelegt. Sie entfernen sich also beide um den selben Betrag L vom Drehzentrum.

α


L

L

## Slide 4

α

L

Achsen

Beispiel:
die Plattform hat sich um den Winkel Alpha gedreht und beide Trittplatten um den Betrag L vom Drehzentrum entfernt.

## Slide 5

v=1s/t

Die Frage die sich nun stellt: wie kann die Strecke L und der Winkel Alpha berechnet werden wenn es geradeaus geht? Zu ermitteln sind hier, bei einer gleichbleibenden Geschwindigkeit (v), die Werte für Alpha und L in Abhängigkeit der Zeit (t) und welche Strecke (s) wird dabei zurück gelegt?

s

t=1

t | s | α | L
0 | 0 | ? | ?
1 | 1 | ? | ?
2 | 2 | ? | ?
3 | 3 | ? | ?
4 | 4 | ? | ?

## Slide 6

t=0

Zum Zeitpunkt t=0, ist noch keine Strecke zurück gelegt worden. Die Plattform ist noch nicht gedreht (Alpha=Null) und beide Trittplatten befinden sich je 2 Einheiten vom Drehzentrum entfernt (L=2).

α=0°

L

t | s | α | L
0 | 0 | 0° | 2

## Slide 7

t=1

Bei t=1, muss sich die Drehplattform bereits um 27° gedreht haben. Die Strecke L hat sich vergrößert. Es ist eine Streckeneinheit in einer Zeiteinheit zurück gelegt worden.

α=atan(1/2)×180/π

L =√(2^2 +1^2)

L

s

t=1

2

Pythagoras

27°

L

2

s

t=1

t | s | α | L
0 | 0 | 0° | 2
1 | 1 | 27° | 2,2

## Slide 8

t=2

45°

α=atan(2/2)×180/π

L =√(2^2 +2^2)

L

s

t=2

t | s | α | L
0 | 0 | 0° | 2
1 | 1 | 27° | 2,2
2 | 2 | 45° | 2,8

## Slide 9

t=3

56°

α=atan(3/2)×180/π

L =√(2^2 +3^2)

t | s | α | L
0 | 0 | 0° | 2
1 | 1 | 27° | 2,2
2 | 2 | 45° | 2,8
3 | 3 | 56° | 3,6

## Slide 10

t=4

63°

Zum Zeitpunkt t=4 ist der Schritt nach Vorne beendet.

α=atan(4/2)×180/π

L =√(2^2 +4^2)

t | s | α | L
0 | 0 | 0° | 2
1 | 1 | 27° | 2,2
2 | 2 | 45° | 2,8
3 | 3 | 56° | 3,6
4 | 4 | 63° | 4,5

## Darstellung der Achsenposition als Graph

Hier werden die Werte für Alpha und L nochmals dargestellt, in Abhängigkeit der Zeit (t) für einen Schritt.

t | s | α | L
0 | 0 | 0° | 2
1 | 1 | 27° | 2,2
2 | 2 | 45° | 2,8
3 | 3 | 56° | 3,6
4 | 4 | 63° | 4,5

α=atan(s/2)×180/π

L =√(2^2 +s^2)

oder auch

L =2/(cos(α))

L

s

2

α

## Schrittfolgen: Achsenpositionen

α

t

L

t

## Schrittfolgen: Geschwindigkeiten und Positionen

α/v

t

L

t

## Schrittfolgen: Beschleunigungen

Es ist ersichtlich, dass die Beschleunigungswerte Spitzen haben, bzw. ein unmittelbarer Richtungswechsel beim Aufsetzen eines Fußes erreicht werden muss.

a

t

a

t

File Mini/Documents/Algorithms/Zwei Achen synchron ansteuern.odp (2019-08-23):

## Virtual Reality Treadmill "Crosswalk"

## Thema: Achsen synchron ansteuern

## Virtual Reality Treadmill "Crosswalk"

## Vorwort

In diesem Dokument geht es darum, wie die Achsen synchron angesteuert werden müssen.

Zu sehen ist, wie die Formeln hergeleitet werden.

## 1. vorhandene Achsen Übersicht

## Vier Achsen sind synchron zu bewegen


β₁

d

b

α

β₂

## 1. vorhandene Achsen Vorwort

## α, β₁, β₂ sowie b müssen synchron zueinander sein

Zu bewegen sind die Achsen α sowie b. Diese Achsen sind synchron zueinander anzusteuern. Zu jeder dieser Achsen existieren anzufahrende Soll-Werte.


## 1. vorhandene Achsen α - Achse

## Die α-Achse dreht die komplette Plattform

- Die α-Achse dreht die gesamte Plattform
- Die α-Achse besitzt einen Encoder mit einer Auflösung von 1200 Pulsen bzw. einer Genauigkeit von
- Diese Achse wird durch vier Gleichstrommotoren angesteuert.

{360°} over {1200}=0,3°

## 1. vorhandene Achsen b - Achse

## Die b-Achse entfernt die Trittplatten voneinander

- Diese Achse erhöht oder verringert den Abstand der zwei Trittplatten zum Drehzentrum hin.
- Bewegt sich diese Achse, so nähern oder entfernen sich die Trittplatten um den selben Betrag vom Drehzentrum weg.
- Die b-Achse besitzt keinen Encoder.
- Die b-Achse wird durch zwei parallel geschaltete Schrittmotoren angetrieben.
- Jeder Schrittmotor besitzt 200 Vollschritte pro Umdrehung.
- Jeder Vollschritt führt zu einer linearen Bewegung um 0,1999mm

Anzahl Zähne der
Zahnscheibe

{20 cdot 2} over {π cdot 200}

Teilung in mm
(bei GT2=2)

Schritte pro
Umdrehung

## Problemstellung

## gegebene Bedingungen

- Nur die α-Achse besitzt einen Encoder
- Für die b Achse gibt es kein Feedback
- Es muss davon ausgegangen werden, dass die Schrittmotoren und die Servomotoren dem Sollwert schnell genug folgen können

## Problemlösung

## Die α-Achse wird die primäre Achse

- Die α-Achse wird die primäre Achse.
- Die b Achse hat sich dem Feedback der α-Achse anzupassen.
- Sollte sich im Praxisversuch herausstellen, dass die b Achse zu langsam ist um der primären Achse zu folgen, so sind entsprechend stärkere Motoren einzusetzen.

Es ist also eine Formel für die Achse b zu erstellen.

## Aufgabenstellung

## Hierfür sind Formeln zu finden

- Die b Achse ist synchron mit der primären α-Achse zu bewegen.
- Für alle Achsen gibt es Delta-Soll-Werte Beispiel: ∆α = 30°,∆b = 8mm
- Alle Achsen müssen gleichzeitig mit der Bewegung beginnen und auch gleichzeitig ihren Soll-Wert erreichen.

## Aufgabenvisualisierung Einleitung

## Die zu fahrende Strecken sind bekannt

Die zu fahrende Strecke einer jeden Achse kann mit Linien verglichen werden, die unterschiedlich lang sind:

∆α-Strecke

∆b-Strecke

## Aufgabenvisualisierung “Pulse”

## Diese “Pulse” müssen synchronisiert werden

Mann kann sich auch folgendes vorstellen: auf jeder Linie sind "Pulse" vorhanden, die die Achse um jeweils eine Einheit weiter bewegen.

∆α-Strecke (17 Pulse)

∆b-Strecke (10 Pulse)

## Aufgabenvisualisierung strecken/stauchen

## Die “Pulse” von β₁ , β₂ , und b verschieben sich

Identische Länge

Damit alle Achsen gleichzeit mit ihrer Bewegung fertig sind, müssen die Linien der sekundären Achse gestreckt werden:

∆α-Strecke (17 Pulse, wird nicht gestreckt)


∆b-Strecke (10 Pulse)

## Formeln Einleitung

## Die “Pulse” sind zu strecken/stauchen

- Die sekundären Achsen müssen der primären Achse folgen.
- Damit die sekundäten Achsen gleichzeitig mit der primären Achse ihre Soll-Position erreichen, sind nur die “Pulse” der sekundären Achsen zu strecken/stauchen.
- Hierzu ist das Verhältniss zwischen dem zu fahrenden Weg (“Pulse”) der sekundären Achsen mit dem zu fahrenden Weg (“Pulse”) der primären Achse ins Verhältnis zu setzen:

{∆Wegstrecke sekundäre Achse} over {∆Wegstrecke primäre Achse}

## Formeln 1. Beispiel

## Die sekundären Achsen bewegen sich halb so schnell

- 1.Beispiel:  Soll sich die primäre Achse um 10 Einheiten bewegen, die sekundären Achsen allerdings nur um 5 Einheiten, so ist das Verhältnis:  Mit anderen Worten: die sekundären Achsen bewegen sich in diesem Beispiel halb so schnell (=0,5) wie die primäre Achse.

{5} over {10}=0,5

## Formeln 2. Beispiel

## Die sekundären Achsen bewegen sich doppelt so schnell

- 2.Beispiel:  Soll sich die primäre Achse um 25 Einheiten bewegen, die sekundären Achsen allerdings nur um 50 Einheiten, so ist das Verhältnis:  Mit anderen Worten: die sekundären Achsen bewegen sich in diesem Beispiel doppelt so schnell (=2) wie die primäre Achse.

{50} over {25}=2

## Formeln „Streck“-Faktoren berechnen

## Diese Faktoren strecken/stauchen die sekundären Achsen

Es muss also, damit alle Achsen gleichzeitig die Soll-Position erreichen, für jede sekundären Achse ein Faktor bestimmt werden.

β₁ Faktor = {∆β₁ Wegstrecke} over {∆α Wegstrecke}

β₂ Faktor = {∆β₂ Wegstrecke} over {∆α Wegstrecke}

b Faktor = {∆b Wegstrecke} over {∆α Wegstrecke}

## Formeln Soll-Position der sekundären Achsen

## Die Soll-Position der sekundären sind damit bekannt

Da die primäre Achse einen Encoder besitzt, kann aufgrund der aktuellen ∆Ist-Position der primären Achse, die ∆Soll-Positionen der sekundären Achsen berechnet werden:

∆β₁ Soll = (∆α Wegstrecke) cdot (β₁ Faktor)

∆β₂ Soll = (∆α Wegstrecke) cdot (β₂ Faktor)

∆b Soll = (∆α Wegstrecke) cdot (b Faktor)

Hinweis: bei “∆α Wegstrecke” handelt es sich um die zurück zu legende Wegstrecke der primären Achse.



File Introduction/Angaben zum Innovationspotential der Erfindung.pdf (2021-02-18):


# EIGENE DARSTELLUNG

# DER ERFINDUNG

## EXPOSEE

### Angaben zum Innovationspotential der Erfindung

## Wasmeier, Peter

### Bedienvorrichtung, um sich in der

virtuellen | Realität | gattungsgemäß
fortbewegen zu können.

## ANGABEN ZUM INNOVATIONSPOTENZIAL DER ERFINDUNG

### Darlegung der Erfindung im Vergleich zum Stand der Technik

Es sind bereits Vorrichtungen bekannt, mit dessen Hilfe sich Personen, bzw. dessen Avatare, in der virtuellen Realität fortbewegen können. Jedoch ist ein bekanntes Problem dieser Lösungen, dass beim Benutzer Schwindel und/oder Unwohlsein entstehen kann, da entweder Bein- und Fußbewegungen durchzuführen sind, die nicht dem Gang des Menschen entsprechen oder die künstliche Fortbewegung per Knopfdruck oder Analogstick herbeigeführt wird. Vorrichtungen, die gezielt mit den Beinen gesteuert werden, erlauben entweder keinen natürlichen Gang, Richtungswechsel, Treppensteigen oder aber die Vorrichtung ist zu groß oder kostspielig.

### technische Realisierbarkeit

Der von mir gewählte Ansatz erlaubt den natürlichen Gang und Treppensteigen durch zwei Trittplatten, die sich auf einer rotierenden Plattform um ein gemeinsames Zentrum drehen und sich von diesem entfernen- oder annähern können. Jeder der Trittplatten kann sich zusätzlich um sich selbst drehen und sich vertikal auf- und ab bewegen. In der Summe sind dabei 6 Achsen beteiligt.

VR-Brille; Vorrichtung

Diese Art des Aufbaus ermöglicht ein natürliches Gehen und verhindert so Schwindel und/oder Unwohlsein beim Benutzer. Auf weniger als 1m² lassen sich natürliche Laufbewegung in alle Richtungen durchführen; darunter auch Schritte zur Seite (sogenannte „sidesteps“) und rückwärts.

Sensoren ermitteln die Laufrichtung und steuern die Achsen entsprechend dem sich in der Luft befindlichem Fuß und ziehen dabei das Standbein in entgegen gerichteter Richtung. Dies sorgt dafür, dass der Benutzer sich immer im Zentrum der Vorrichtung befindet. Über ein optional erhältliches Zubehör wird es auch möglich sein sich in der virtuellen Realität zu setzen, beispielsweise auf eine virtuelle Parkbank oder auch dem Fahrersitz eines PKWs.

### mögliche Einsatzgebiete

Die Vorrichtung ist für die Unterhaltung gedacht und kann in VR-Spielhallen sowie auch Zuhause genutzt werden. Ein weiteres mögliches Einsatzgebiet wäre ein Fitnesscenter: statt auf einem Laufband zu rennen, kann diese Vorrichtung das Rennen durch virtuelle Städte oder auch Landschaften simulieren, so vergeht die Zeit auf dem Laufband schneller und interessanter.

Denkbar sind auch virtuelle Besuche von Museen, Wohnungs- oder Hausbesichtigungen oder auch der Besuch von Sehenswürdigkeiten.

Abbildung 1 Schemazeichnung

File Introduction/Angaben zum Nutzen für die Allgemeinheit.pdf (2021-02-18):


# EIGENE DARSTELLUNG DER ERFINDUNG

## EXPOSEE

### Angaben zum Nutzen für die Allgemeinheit

## Wasmeier, Peter

### Bedienvorrichtung, um sich in der

virtuellen | Realität | gattungsgemäß
fortbewegen zu können.

## ANGABEN ZUM NUTZEN FÜR DIE ALLGEMEINHEIT

Zum Thema Umweltschutz, Ressourcenschonung, Arbeitssicherung sowie Schaffung von Arbeitsplätzen kann diese Vorrichtung keinen Beitrag leisten.

### Vorteile für die Verbraucher

Diese Vorrichtung ermöglicht es dem Verbraucher sich artgerecht in der virtuellen Welt zu bewegen und erhöht so die Immersion für den Verbraucher. Im Gegensatz zu früher werden keine Knöpfe mehr an einem Controller gedrückt, um sich in der virtuellen Welt fortzubewegen. Die Beine bzw. die Schritte selbst werden zum Controller, um die Laufrichtung und Geschwindigkeit zu bestimmen. Dadurch, dass diese Vorrichtung den Benutzer auch stets im Mittelpunkt auf der Plattform hält, sind Möbel und Wände kein Hindernis mehr. Mit einem knappen Quadratmeter findet diese Vorrichtung auch in einer kleinen Wohnung Platz.

In Zeiten der Digitalisierung, Smartphones und Couchsurfing, bietet diese Vorrichtung die Möglichkeit wieder körperlich fit zu werden. Anstatt also vom Sofa aus einem Computerspiel nachzugehen, erhält man nun die Möglichkeit sich tatsächlich, spielerisch, in einer virtuellen Welt aufzuhalten. Statt einem echten Spaziergang im Regen/schlechtem/kaltem Wetter, bietet sich nun die Möglichkeit diesen Spaziergang temperiert in einer künstlichen Umgebung (Bsp. Wohnzimmer) zu genießen. Aktion-/Abenteuer Spiele in VR werden einen ganz neuen Level erreichen, da nunmehr auch körperliche Fitness gefordert wird.

Es wird nicht mehr notwendig sein sich Tastenkombinationen zu merken, die bisher notwendig sind, um sich in der virtuellen Realität oder in Computerspielen zu bewegen.

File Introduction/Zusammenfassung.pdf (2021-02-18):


# EIGENE DARSTELLUNG

# DER ERFINDUNG

## EXPOSEE

### Zusammenfassung der Erfindung

## Wasmeier, Peter

## Bedienvorrichtung, um sich in der virtuellen Realität gattungsgemäß

fortbewegen zu können.

FORTBEWEGUNG IN DER VIRTUELLEN REALITÄT

DIE ERFINDUNG

Eine Vorrichtung, mit dessen Hilfe sich ein Benutzer mit seinen Beinen in der virtuellen Realität (VR) fortbewegen kann.

DER ERFINDER

Peter Wasmeier
Singen

DIE PROBLEMSTELLUNG / AUSGANGSLAGE

Um sich, bzw. seinen Avatar, in einem Computerspiel fortbewegen zu können sind bisher verschiedene Tasten zu Drücken oder das Neigen eines Joysticks notwendig. Manch' einer verwendet auch eine Computermaus.
Wir sind es nicht anders gewohnt und hinterfragen diese Art der Fortbewegung in Computerspielen nicht wirklich. Gekonnt wird mit einem Mausklick ein Moorhuhn nach dem anderen abgeschossen.

Wer in ein Computerspiel eintauchen möchte, muss heutzutage eine Virtuelle-Realität-Brille, kurz VR-Brille, aufsetzen. Eine VR-Brille ermöglicht es eine künstliche Umgebung (die Spielewelt) in allen drei Dimensionen wahrzunehmen. Der Vergleich mit einem 3D-Kinofilm ist unangebracht, bzw. nicht zu vergleichen, da der Benutzer tatsächlich den Eindruck hat, sich in dieser Umwelt zu befinden, statt diese, wie im 3D-Kino, nur zu Betrachten. Er wird also selbst zum Avatar.

Dennoch bleibt die Frage nach der eigentlichen Fortbewegung. Wie schön wäre es, wenn hierzu die Beine benutzt werden könnten, so wie es auch bei einem Spaziergang gemacht wird: ein Schritt nach dem anderen in die gewünschte Richtung.

Um sich in einem VR-Computerspiel fortbewegen zu können werden heute noch immer Kontroller verwendet, die mit den Händen oder den Füßen gesteuert werden. Der Spieler selbst sitzt oder steht dabei und hat eine VR-Brille auf, die die virtuelle Umgebung darstellt. Sofern ein VR-Spiel im Stehen gespieltwird, muss der Benutzerdarauf achten nicht instinktiv seine Füße zum Gehen zu nutzen. Andernfalls läuft er Gefahr gegen ein Hindernis in seiner realen Wohnung zu stoßen.

Da diese Art der Fortbewegung in VR nicht dem natürlichen Gang des Menschen entspricht, führt dies bei einigen Personen oft zu Schwindel und/oder Orientierungslosigkeit.

Hinzu kommen die vielen Knöpfen die zu drücken sind (und man sich merken muss) um: vorwärts, rückwärts, seitwärts, sich im- oder entgegen des Uhrzeigersinnes zu drehen. Ganz zu Schweigen von den Tastenkombinationen, um zu rennen, ducken, schleichen, etc.

Dies zusammen kann zu Unzufriedenheit und Frustration führen, die das Spieleerlebnis trübt.

DIE INNOVATION

Um sich in der virtuellen Realität frei bewegen zu können, muss eine Vorrichtung existieren, die eine Person unbemerkt auf der Stelle gehen lässt. Somit läuft dieser nicht Gefahr gegen ein Hindernis zu stoßen.

Wie kommt man voran, wenn man stets auf der Stelle geht?

VR-Brille

Der von mir gewählte Ansatz ist ungewöhnlich und das erste „Laufband“ seiner Art. Entgegen anderen Lösungen, die bereits existieren, wird das von mir erdachte Gerät nicht nur alle Bewegungsrichtungen erlauben, sondern auch Treppen und Fahrstühle können künstlich simuliert werden.

Sensoren ermitteln die Laufrichtung und steuern die Achsen entsprechend dem sich in der Luft befindlichem Fuß und ziehen dabei das Standbein in entgegen gerichteter Richtung (oder auch nach unten/oben). Dies sorgt dafür, dass der Benutzer sich immer im Zentrum der Vorrichtung befindet. Über ein optional erhältliches Zubehör wird es auch möglich sein sich in der virtuellen Realität zu setzen, beispielsweise auf eine virtuelle Parkbank oder auch dem Fahrersitz eines PKWs.

Somit entsteht der Eindruck, tatsächlich in der virtuellen Umgebung bzw. dem Computerspiel artgerecht gehen zu können.

Vorrichtung

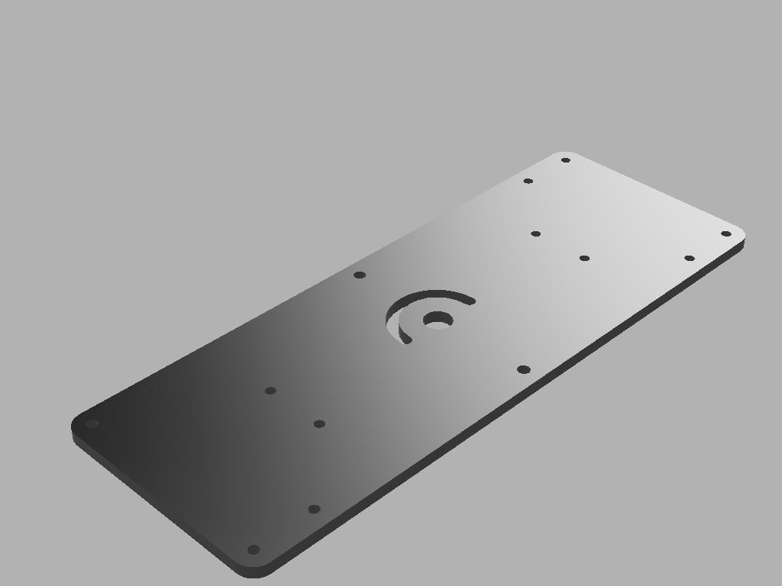
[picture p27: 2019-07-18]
Mini/3D-Files/special/Footplate/Footplate.png

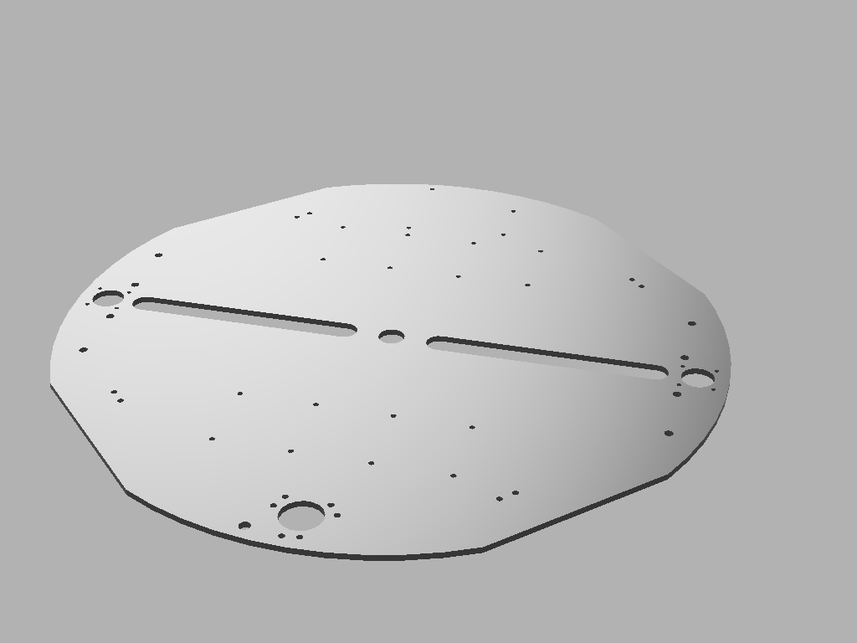
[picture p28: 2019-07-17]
Mini/3D-Files/special/Baseplate/Baseplate-3mm.png

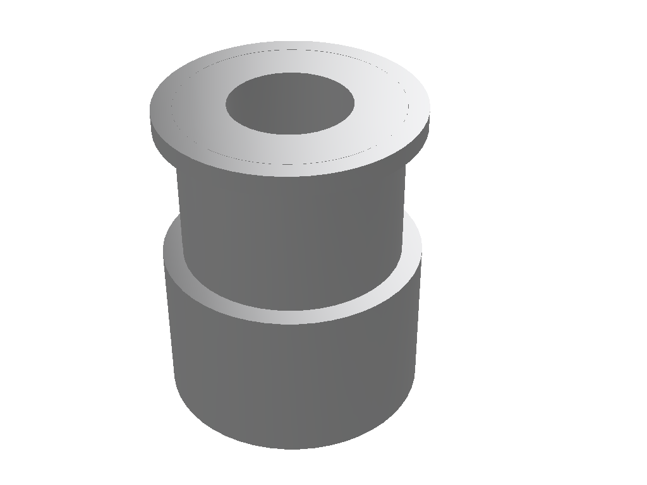
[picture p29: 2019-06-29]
Mini/3D-Files/general/Pulley, 16 tooths, drill hole 6mm/Pulley, 16 tooths, drill hole 6mm.png

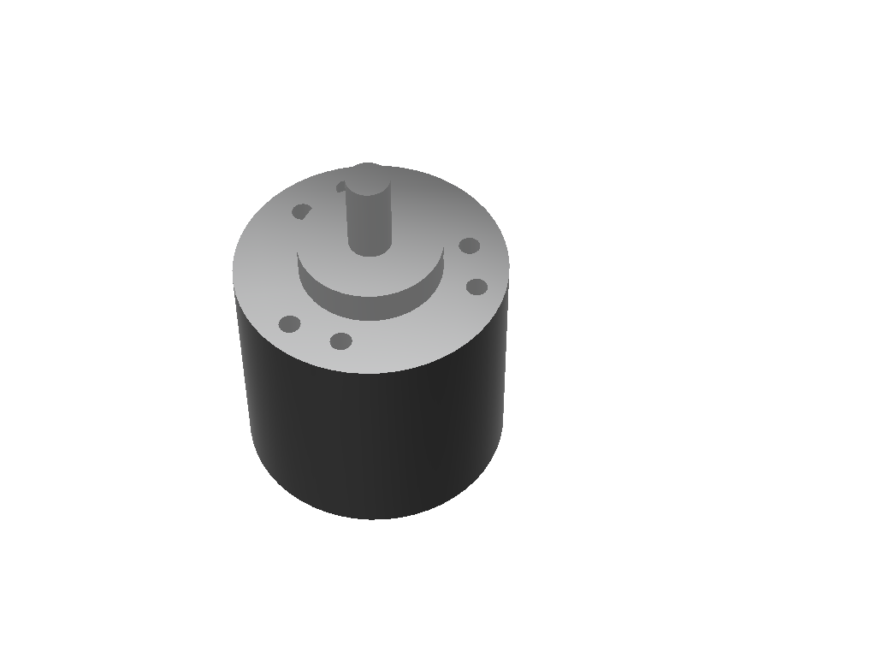
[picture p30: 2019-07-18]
Mini/3D-Files/general/Encoder/Encoder.png

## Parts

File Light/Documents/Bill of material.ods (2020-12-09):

 |  |  |  |  | Bill of material (BOM)
Item # | Quantity | in Stock | Description | Unit price | Total price | Group | Link/Supplier
1 | 1 | 1 | Turntable, 800mm | 159,85 € | - € | Mechanic | https://www.amazon.de/dp/B06XC2KSPV?psc=1&ref=ppx_pop_dt_b_product_details
2 | 1 | 0 | Turntable washer, 1mm | 32,80 € | 32,80 € | Laser | https://www.laserteile4you.de/app/offer/158880/quote
3 | 1 | 0 | Bottom cover, 1mm | 32,02 € | 32,02 € | Laser | https://www.laserteile4you.de/app/offer/158880/quote
4 | 2 | 0 | Cover plate horizontal axis, 5mm | 15,17 € | 30,35 € | Laser | https://www.laserteile4you.de/app/offer/158880/quote
5 | 1 | 0 | Base plate, 5mm | 89,93 € | 89,93 € | Laser | https://www.laserteile4you.de/app/offer/158880/quote
6 | 1 | 0 | Top cover, 4mm | 70,59 € | 70,59 € | Laser | https://www.laserteile4you.de/app/offer/158880/quote
7 | 2 | 0 | Footplate, 5mm | 15,34 € | 30,68 € | Laser | https://www.laserteile4you.de/app/offer/158880/quote
8 | 1 | 1 | Shipping cost for item #2-#7 | 198,46 € | - € | Shipping | https://www.laserteile4you.de/app/offer/158880/quote
9 | 1 | 0 | Fabric frame, 3086mm |  | - € | Textil
10 | 1 | 0 | Shipping cost for item #10 - #11 | 6,90 € | 6,90 € | Shipping | https://www.dold-mechatronik.de/
11 | 4 | 0 | TBS16, 350mm | 16,00 € | 64,00 € | Mechanic | https://www.dold-mechatronik.de/Linearfuehrung-Supported-Rail-TBS16-350mm-lang
12 | 4 | 0 | TBR16UU | 8,90 € | 35,60 € | Mechanic | https://www.dold-mechatronik.de/Linearlager-16mm-TBR16UU-offen-Spiel-einstellbar
13 | 2 | 2 | Worm gear motor | 31,00 € | - € | Electric | https://www.amazon.de/gp/product/B0788B73HP/ref=ppx_yo_dt_b_asin_title_o05_s00?ie=UTF8&psc=1
14 | 1 | 1 | Encoder | 16,99 € | - € | Electric | https://www.amazon.de/gp/product/B015GYY7XU/ref=ppx_od_dt_b_asin_title_s01?ie=UTF8&psc=1
15 | 1 | 0 | Toothed belt | 3,23 € | 3,23 € | Mechanic | https://www.amazon.de/gp/product/B07D4GCYXW/ref=ox_sc_act_title_1?smid=AHL08YKX3LDJ0&psc=1
16 | 2 | 0 | Outer rope pulley | 1,69 € | 3,38 € | 3D print | 3D Printer
17 | 1 | 0 | Motor rope pulley | 1,19 € | 1,19 € | 3D print | 3D Printer
18 | 1 | 0 | Center rope pulley | 1,17 € | 1,17 € | 3D print | 3D Printer
19 | 1 | 1 | Slipring | 17,99 € | - € | Electric | https://www.amazon.de/gp/product/B07FL8LDYN/ref=ppx_yo_dt_b_asin_title_o01_s00?ie=UTF8&psc=1
20 | 1 | 0 | Middle rope pulley | 0,92 € | 0,92 € | 3D print | 3D Printer
21 | 2 | 2 | Motor N2830 | 14,99 € | - € | Electric | https://www.amazon.de/gp/product/B07JKJQ9TG/ref=ppx_yo_dt_b_asin_title_o09_s00?ie=UTF8&psc=1
22 | 2 | 2 | Encoder AS5600 | 6,53 € | - € | Electric | https://www.amazon.de/gp/product/B088PJF9WV/ref=ppx_yo_dt_b_asin_title_o00_s00?ie=UTF8&psc=1
23 | 1 | 1 | Odrive V3.6 | 129,00 € | - € | Electric | https://eu.odriverobotics.com/shop/odrive-v36
24 | 1 | 1 | Shipping cost for item #23 | 18,45 € | - € | Shipping | https://eu.odriverobotics.com/shop/odrive-v36
25 | 1 | 1 | Arduino Uno | 7,99 € | - € | Electric | https://www.amazon.de/gp/product/B01MDJA464/ref=ox_sc_act_title_1?smid=A1X7QLRQH87QA3&psc=1
26 | 23 | 23 | Odrive Pin | - € | - € | Screw | Part of item #23
27 | 2 | 0 | Holder magnet |  | - € | 3D print | 3D Printer
28 | 2 | 0 | Lid motor |  | - € | 3D print | 3D Printer
29 | 2 | 0 | Motor frame |  | - € | 3D print | 3D Printer
30 | 29 | 0 | Adapter 4mm to 3mm | 0,01 € | 0,15 € | 3D print | 3D Printer
31 | 12 | 0 | DIN 912, M3x10 | 0,24 € | 2,87 € | Screw | https://www.amazon.de/gp/product/B07H4JW4GD/ref=ox_sc_act_title_1?smid=A9TBW19CJ4SDE&psc=1
32 | 19 | 0 | DIN 985, M5 | 0,12 € | 2,28 € | Screw | https://www.amazon.de/gp/product/B08CJQYBBH/ref=ox_sc_act_title_1?smid=AHDWMK444VJ1S&psc=1
33 | 3 | 0 | DIN 912, M5x20 | 0,27 € | 0,82 € | Screw | https://www.amazon.de/gp/product/B07TX28YLK/ref=ox_sc_act_title_1?smid=A3P7AXYBBIBGQZ&psc=1
34 | 16 | 0 | DIN 912, M5x15 | 0,35 € | 5,58 € | Screw | https://www.amazon.de/gp/product/B00SN35Y9I/ref=ox_sc_act_title_1?smid=A1P9DCA88LI1WF&psc=1
35 | 3 | 0 | DIN 912, M5x8 | 0,74 € | 2,22 € | Screw | https://www.amazon.de/gp/product/B07KKDG8HB/ref=ox_sc_act_title_1?smid=A3JM6MQKK7VE65&psc=1
36 | 35 | 0 | ISO 10642, M3x6 | 0,30 € | 10,41 € | Screw | https://www.amazon.de/gp/product/B07C6S4Z2T/ref=ox_sc_act_title_1?smid=A3CZZ1IZ45HRES&psc=1
37 | 4 | 0 | ISO 10642, M3x10 | 0,40 € | 1,59 € | Screw | https://www.amazon.de/gp/product/B07DHNP5KF/ref=ox_sc_act_title_1?smid=A1WLWSDG4A6FOP&psc=1
38 | 1 | 0 | 3th support | 0,50 € | 0,50 € | 3D print | 3D Printer
39 | 8 | 8 | DIN 912, M3x5 | 0,36 € | - € | Screw | https://www.amazon.de/gp/product/B08DK2P4NP/ref=ppx_yo_dt_b_asin_title_o04_s00?ie=UTF8&psc=1
40 | 24 | 0 | DIN 945, M4 | 0,26 € | 6,23 € | Screw | https://www.amazon.de/gp/product/B08CJ9H6BG/ref=ox_sc_act_title_1?smid=AHDWMK444VJ1S&psc=1
41 | 4 | 0 | MF105ZZ, 5x10x4mm | 1,11 € | 4,42 € | Mechanic | https://www.amazon.de/gp/product/B07MF31X8Y/ref=ppx_yo_dt_b_asin_title_o06_s00?ie=UTF8&psc=1
42 | 24 | 0 | DIN 912, M4x15 | 0,19 € | 4,47 € | Screw | https://www.amazon.de/gp/product/B00SN32TBO/ref=ox_sc_act_title_1?smid=A1P9DCA88LI1WF&psc=1
43 | 8 | 8 | DIN 912, M2x4 | - € | - € | Screw | Part of item #21
44 | 8 | 8 | Locating pin, 5x40mm | 0,58 € | - € | Mechanic | https://www.amazon.de/gp/product/B07DGY7PZV/ref=ppx_yo_dt_b_asin_title_o06_s00?ie=UTF8&psc=1
45 | 2 | 0 | Idler pulley, 5mm | 1,82 € | 3,65 € | Mechanic | https://www.amazon.de/gp/product/B0762FV13M/ref=ox_sc_act_title_1?smid=A5QX2SUPA7LK7&psc=1
46 | 4 | 0 | Pulley, 5mm | 1,80 € | 7,19 € | Mechanic | https://www.amazon.de/gp/product/B01LZIP1M8/ref=ppx_yo_dt_b_asin_title_o00_s00?ie=UTF8&psc=1
47 | 8 | 8 | Set collar, 5mm | 1,94 € | - € | Mechanic | https://www.amazon.de/gp/product/B01KFYZLSG/ref=ppx_yo_dt_b_asin_title_o00_s00?ie=UTF8&psc=1
48 | 8 | 0 | ISO 10642, M8x30 | 1,04 € | 8,30 € | Screw | https://www.amazon.de/gp/product/B07S5YK97K/ref=ox_sc_act_title_1?smid=A3JM6MQKK7VE65&psc=1
49 | 2 | 2 | Pulley, 20 tooths, 5mm | 1,00 € | - € | Mechanic | https://www.amazon.de/gp/product/B085MK4LQZ/ref=ox_sc_act_title_1?smid=A1BV4N88UHB8BY&psc=1
50 | 1 | 0 | Wheel, 50mm, 5mm |  | - € | 3D print | 3D Printer
51 | 1 | 1 | Flange shaft, 3.17mm | 3,77 € | - € | Mechanic | https://www.amazon.de/gp/product/B07S492QGK/ref=ppx_yo_dt_b_asin_title_o04_s00?ie=UTF8&psc=1
52 | 1 | 1 | Wheel, 50mm, 12mm |  | - € | 3D print | 3D Printer
53 | 1 | 0 | Wheel, 50mm, 10mm |  | - € | 3D print | 3D Printer
54 | 2 | 0 | Cable chain, Start | 0,12 € | 0,24 € | 3D print | 3D Printer
55 | 2 | 0 | Cable chain, End | 0,06 € | 0,12 € | 3D print | 3D Printer
56 | 1 | 0 | Microswitch | 5,19 € | 5,19 € | Electric | https://www.amazon.de/gp/product/B00LFLG08E/ref=ox_sc_saved_title_3?smid=A3VDFIOASBU8U5&psc=1
57 | 1 | 0 | Flange shaft, 6mm | 1,50 € | 1,50 € | Mechanic | https://www.amazon.de/gp/product/B07XM1XKSK/ref=ppx_yo_dt_b_asin_title_o08_s00?ie=UTF8&psc=1
58 | 40 | 0 | Cable chain, Middle | 0,05 € | 2,00 € | 3D print | 3D Printer
59 | 2 | 2 | Magnet | - € | - € | Mechanic | Part of item #22
60 | 1 | 0 | Cable duct | - € | - € | 3D print | 3D Printer
61 | 1 | 1 | Pulley, 60 tooths, 5mm | 6,31 € | - € | Mechanic | https://www.amazon.de/gp/product/B074V7HVHB/ref=ppx_yo_dt_b_search_asin_title?ie=UTF8&psc=1
62 | 5 | 0 | Distance holder, 47.5mm |  | - € | 3D print | 3D Printer
63 | 16 | 0 | ISO 19642, M5x16 |  | - €
64 | 8 | 0 | ISO 10642, M4x14 |  | - €
65 | 8 | 0 | DIN 912, M4x10 |  | - €
66 | 2 | 0 | Belt holder |  | - € | 3D print | 3D Printer
67 | 2 | 2 | L298N Stepper motor driver | 3,20 € | - € | Electric | https://www.amazon.de/gp/product/B077YC3JX9/ref=ppx_yo_dt_b_asin_title_o00_s01?ie=UTF8&psc=1
68 | 1 | 1 | 50wr5j | - € | - € | Electric | Part of item #23

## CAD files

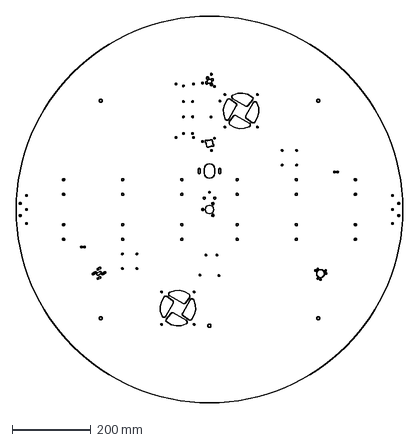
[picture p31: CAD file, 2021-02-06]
Light/3D-Files/special/Baseplate/#5 Base plate, 5mm-1.dxf
980.0 x 980.0 mm

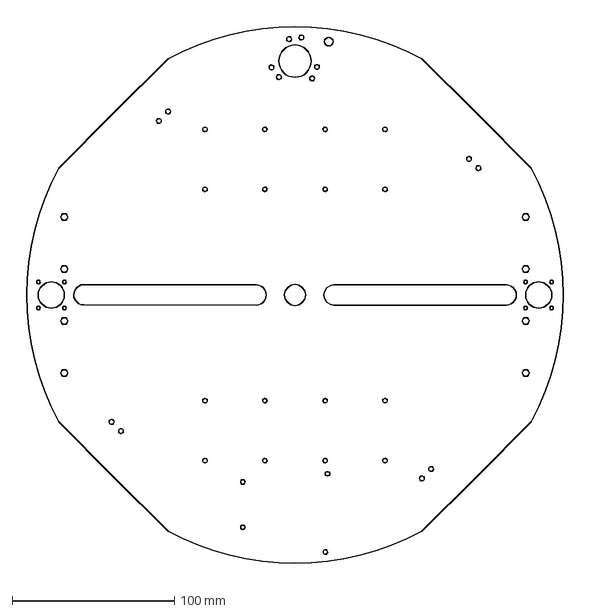
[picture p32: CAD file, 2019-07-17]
Mini/3D-Files/special/Baseplate/Baseplate-3mm.dxf
343.1 x 343.1 mm

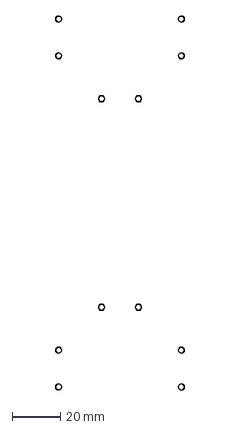
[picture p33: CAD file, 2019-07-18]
Mini/3D-Files/special/Footplate/Footplate.dxf
53.4 x 155.3 mm

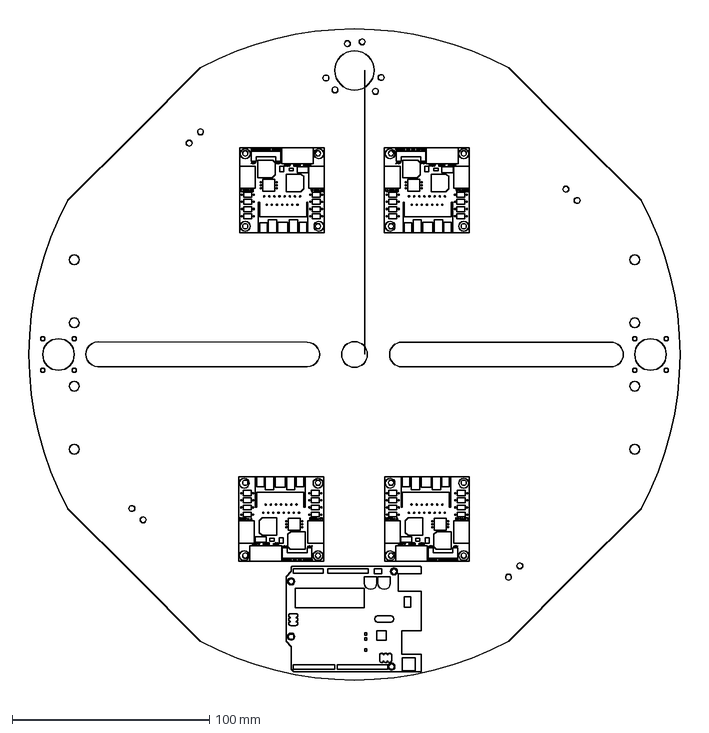
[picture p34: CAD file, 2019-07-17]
Mini/wiring/Base/Baseplate.dxf
343.1 x 343.1 mm

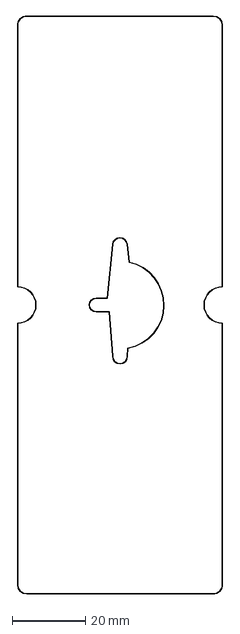
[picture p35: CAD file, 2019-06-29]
Mini/wiring/Footplate/Footplate.dxf
56.0 x 158.0 mm

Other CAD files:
Mini/Code/VR-Crosswalk-Windows/uMain.obj
Mini/Code/VR-Crosswalk-Windows/VRCrosswalkMini.obj
Mini/3D-Files/general/Arduino Uno/Arduino Uno.f3d
Mini/3D-Files/general/Encoder/Encoder.f3d
Mini/3D-Files/general/PCB Spacer M3x5mm/PCB Spacer M3x5mm.f3d
Mini/3D-Files/general/Pulley, 16 tooths, drill hole 6mm/Pulley, 16 tooths, drill hole 6mm.f3d
Mini/3D-Files/general/Pulley, 20 tooths, drill hole 4mm/Pulley, 20 tooths, drill hole 4mm.f3d
Mini/3D-Files/special/Baseplate/Baseplate-3mm.f3d
Mini/3D-Files/special/Footplate/Footplate.f3d

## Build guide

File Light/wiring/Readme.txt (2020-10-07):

In this folder, there is the wiring and the PCBs of the "VR-Crosswalk-Light".

The folder "Base" contains the main wiring, without the footplates. The "Base" share an I2C bus and voltage supply with both "Footplate(s)".

The folder "Footplate" is just for a single foot (you will need two of them, one for each foot). Each footplate is connected via I2C and voltage supply with the "Base".

To open these files, you have to use the program "fritzing".

You can download "fritzing" here:

http://www.fritzing.org/

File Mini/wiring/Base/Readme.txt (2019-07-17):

In this folder, there is the main wiring of the "VR-Crosswalk-Mini".

Files:
	"Arduino Shield.fzz"
	The Arduino might need a shield, so that the wiring is more easier.

	"Base.dxf"
	This will be another PCB, mounted on the baseplate. But not finished yet.

	"Overview.fzz"
	This is a overview of the wiring, without PCBs. This is just an overview to inform which wire goes where.

Remarks:
Right now, it is not clear if the "Arduino Shield.fzz" will be used or, later on, the "Base.dxf/fzz".

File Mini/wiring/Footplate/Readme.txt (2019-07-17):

This is the wiring and PCB of the footplate.

Files:
	"Footplate.fzz"
	The fritzing file with wiring diagram.
        You can download "fritzing" here: http://www.fritzing.org/

	"Footplate.svg"
	The PCB ground plate, done with Inkscape.
        You can download "Inkscape" here: https://inkscape.org/

	"Footplate.dxf"
	The outline of the footplate.

	"Footplate.png"
	An image of the top side of the footplate.

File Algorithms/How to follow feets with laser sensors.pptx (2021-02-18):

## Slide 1

## Foot in center of the footplate

Six VL6180X sensors reports the amount of reflection (called „signal strength“ or „signal rate“ in Mcps) of the foot above them.

Footplate

50%

90%

90%

VL6180X sensor, reporting 90% reflection

The foot in in the center of the footplate

90%

90%

50%

## Foot moving forward

Instead of 50%, it is suddenly 80% reflection

When the foot is moving forward, the reflection of the upper VL6180X sensor reports more reflection and the bottom sensor reports less.
Now it is time to move the footplate forward until the upper and lower sensor reports the same amount of reflection.

80%

90%

90%

90%

90%

20%

Instead of 50%, it is suddenly 20% reflection

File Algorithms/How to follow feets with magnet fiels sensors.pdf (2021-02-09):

# Virtual Reality Treadmill "Crosswalk"

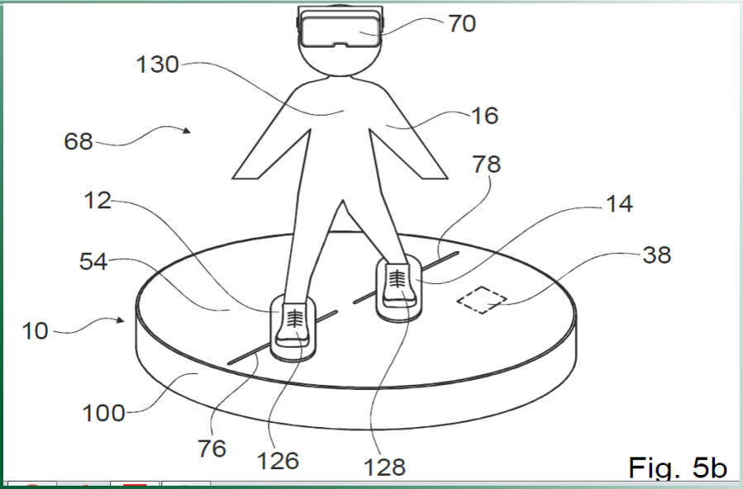
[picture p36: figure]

# Foot following device

# Virtual Reality Treadmill "Crosswalk"

This document will decribe the math stuff to figure out where the foot is located above a footplate by using magnetic field sensors and a magnet.

# Overview of “Crosswalk-Mini”

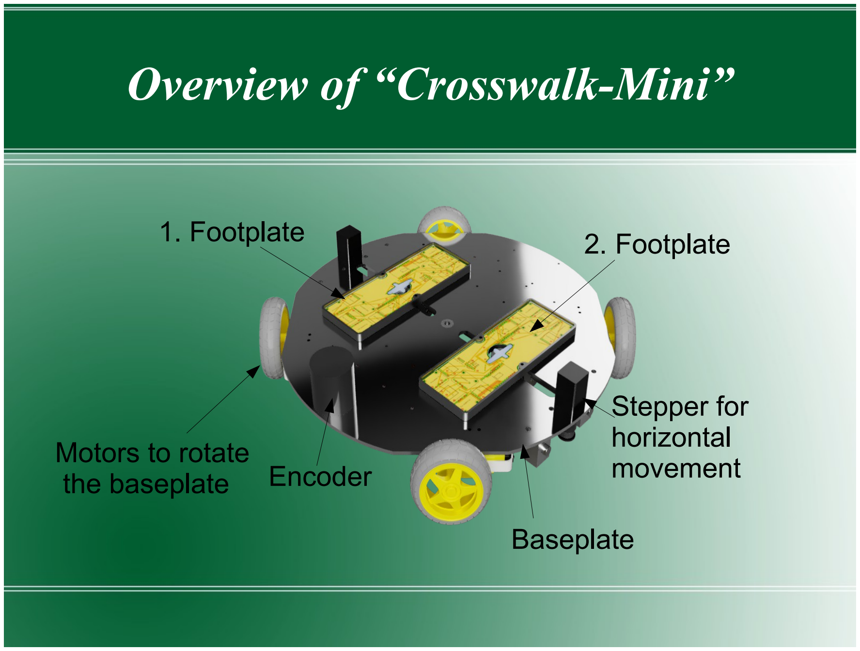
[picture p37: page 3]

d

1. Footplate | 2. Footplate

Stepper for
horizontal
movement Motors to rotate
the baseplate

Baseplate

Encoder

# Where's the foot?

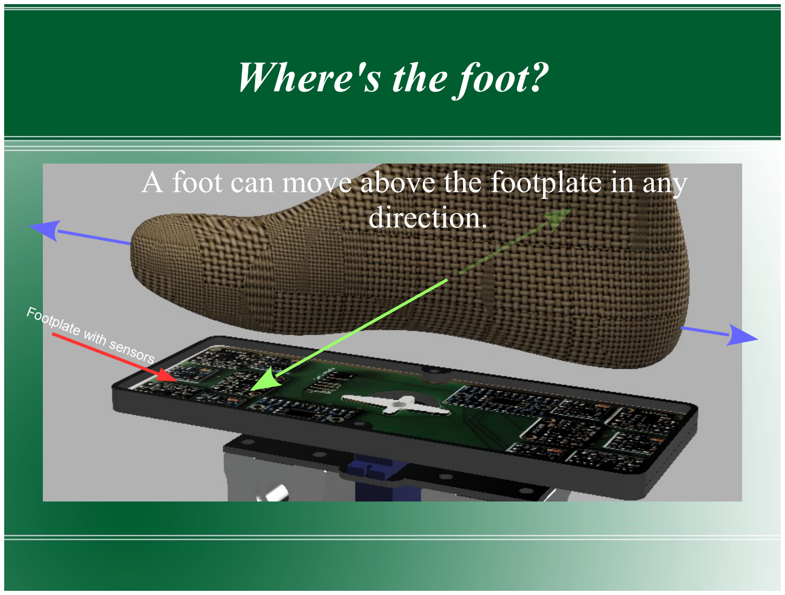
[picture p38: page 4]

## A foot can move above the footplate in any

direction.

Footplate with sensors

# Footplate with magnetic field sensors

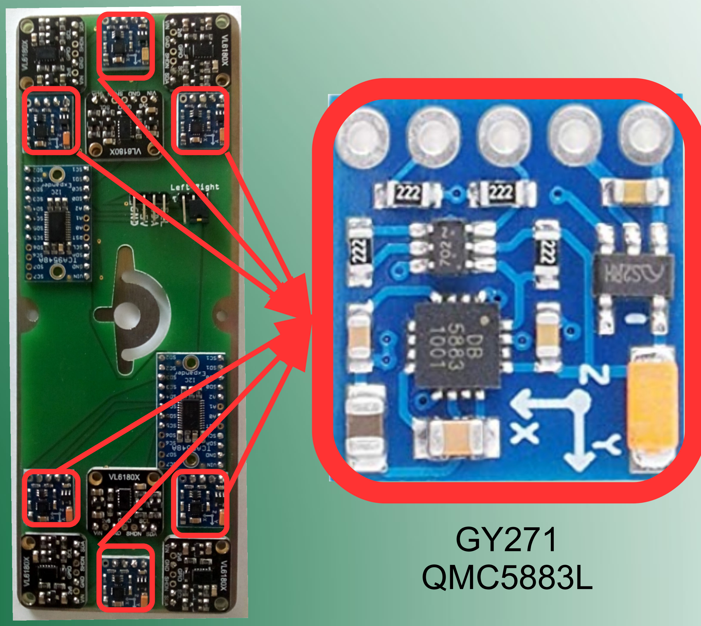
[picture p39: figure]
GY271 QMC5883L

# Magnet in each foot orthosis

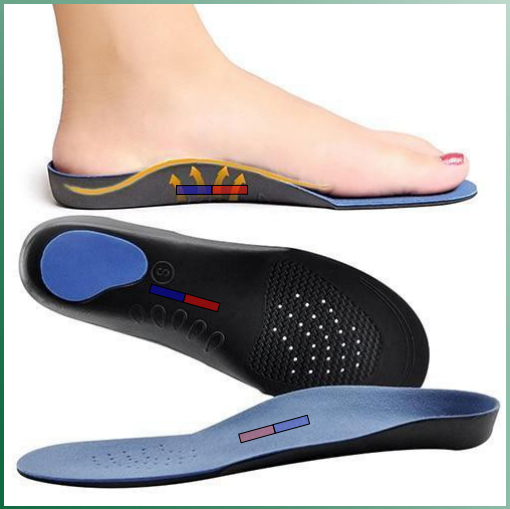
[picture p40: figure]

# Looking for north and south pole 1/2

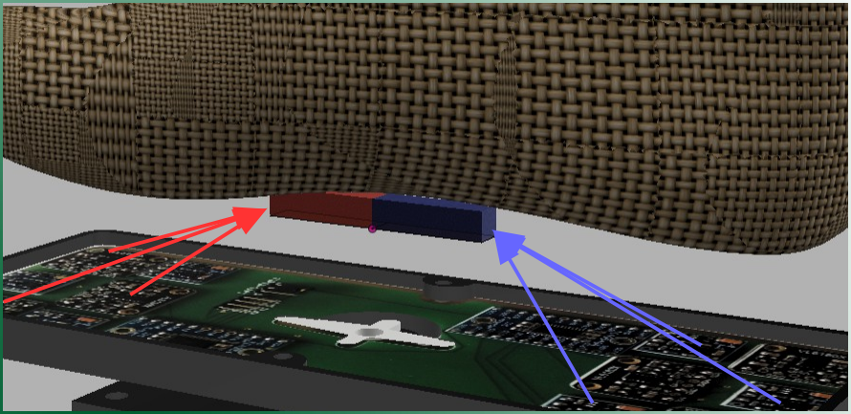
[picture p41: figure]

# Looking for north and south pole 2/2

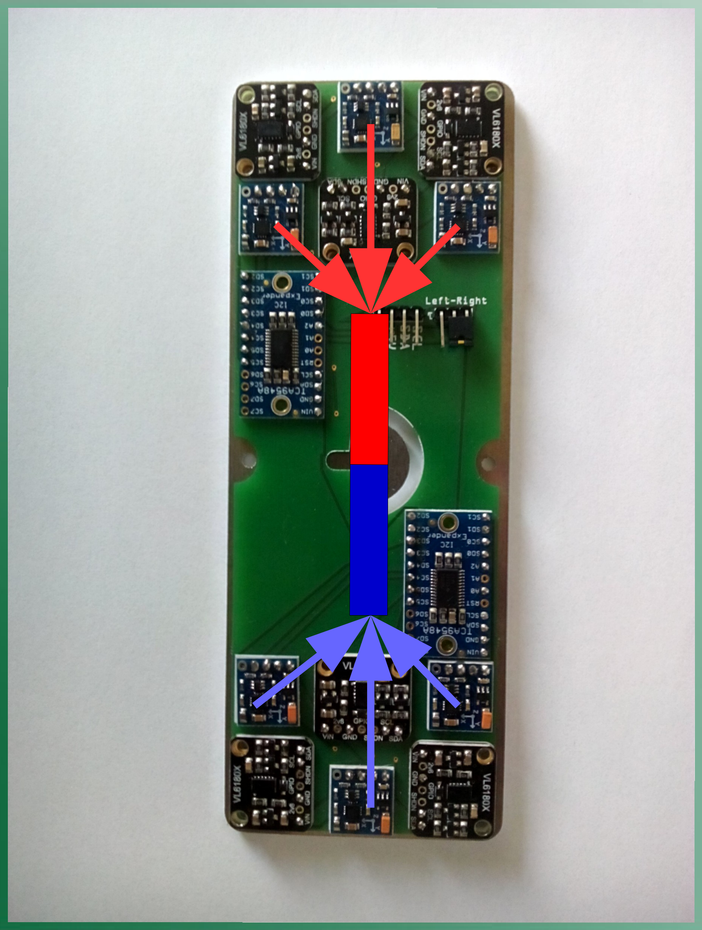
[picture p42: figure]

# coordinate system of the footplate

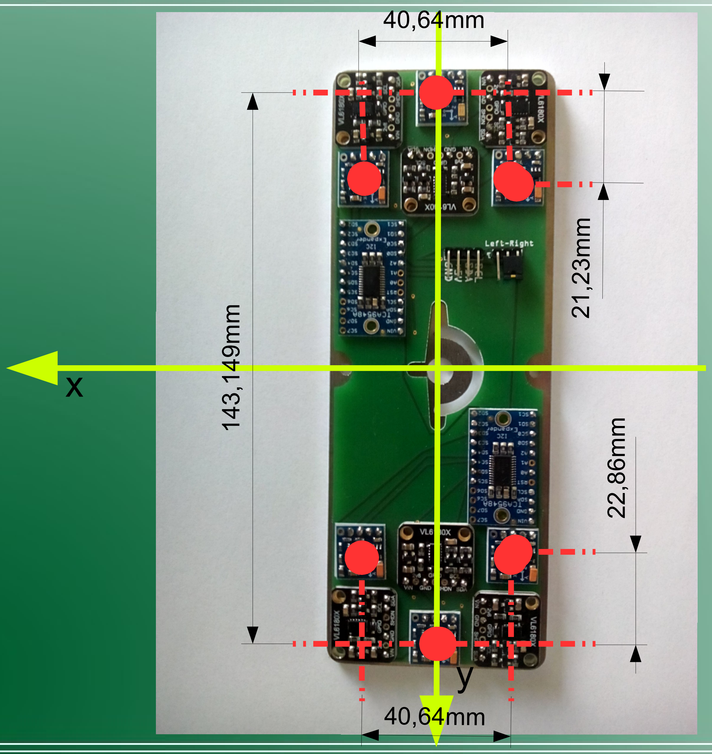
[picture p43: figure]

# up to three Intersections:

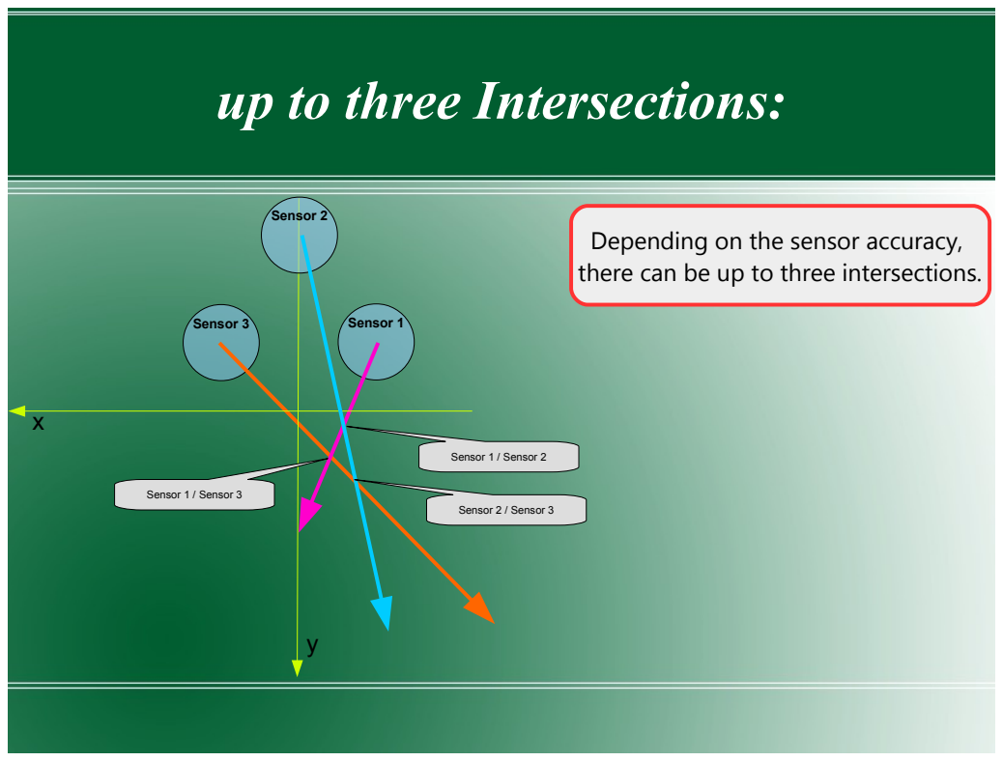
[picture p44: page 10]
Sensor 3; Sensor 1; Sensor 1 / Sensor 2; Sensor 2; Sensor 2 / Sensor 3; Sensor 1 / Sensor 3

Depending on the sensor accuracy,
there can be up to three intersections.

# Intersection of Sensor 1 and 3

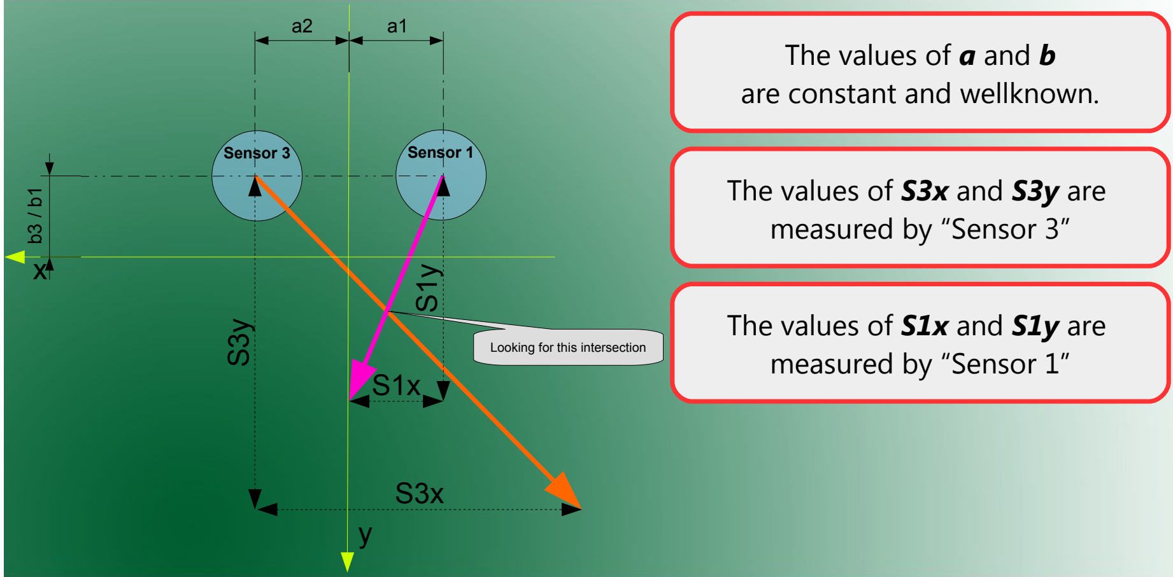
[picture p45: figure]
Sensor 3; Sensor 1; Looking for this intersection; The values of a and b are constant and wellknown.; The values of S3x and S3y are measured by “Sensor 3”; The values of S1x and S1y are measured by “Sensor 1”

# Intersection of Sensor 1 and 2

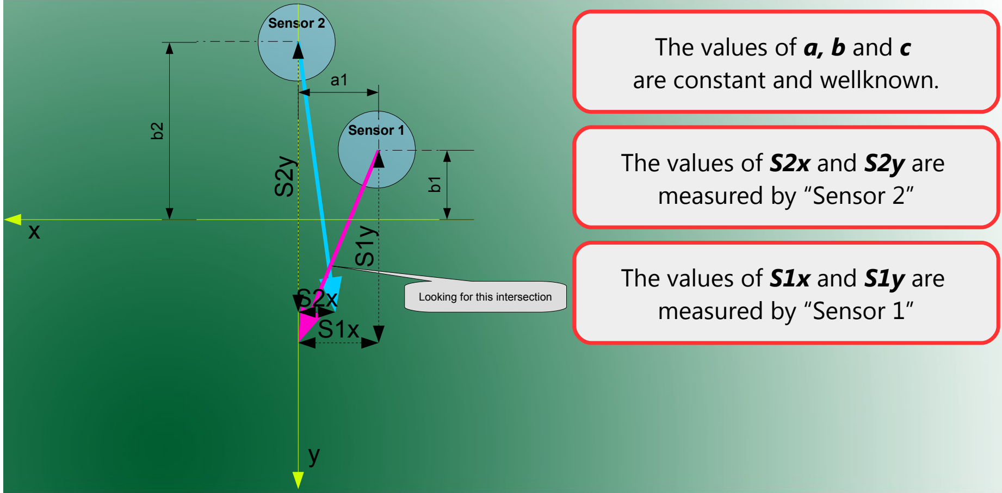
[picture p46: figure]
Sensor 2; Sensor 1; Looking for this intersection; The values of a, b and c are constant and wellknown.; The values of S2x and S2y are measured by “Sensor 2”; The values of S1x and S1y are measured by “Sensor 1”

# Intersection of Sensor 2 and 3

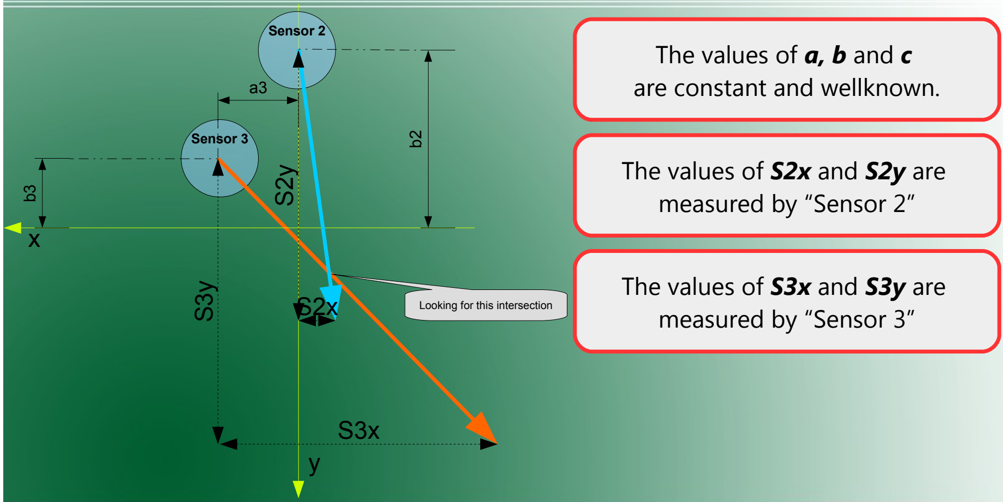
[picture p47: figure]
Sensor 3; Looking for this intersection; The values of a, b and c; are constant and wellknown.; The values of S2x and S2y are measured by “Sensor 2”; The values of S3x and S3y are measured by “Sensor 3”; Sensor 2

# linear equation, looking for “c”

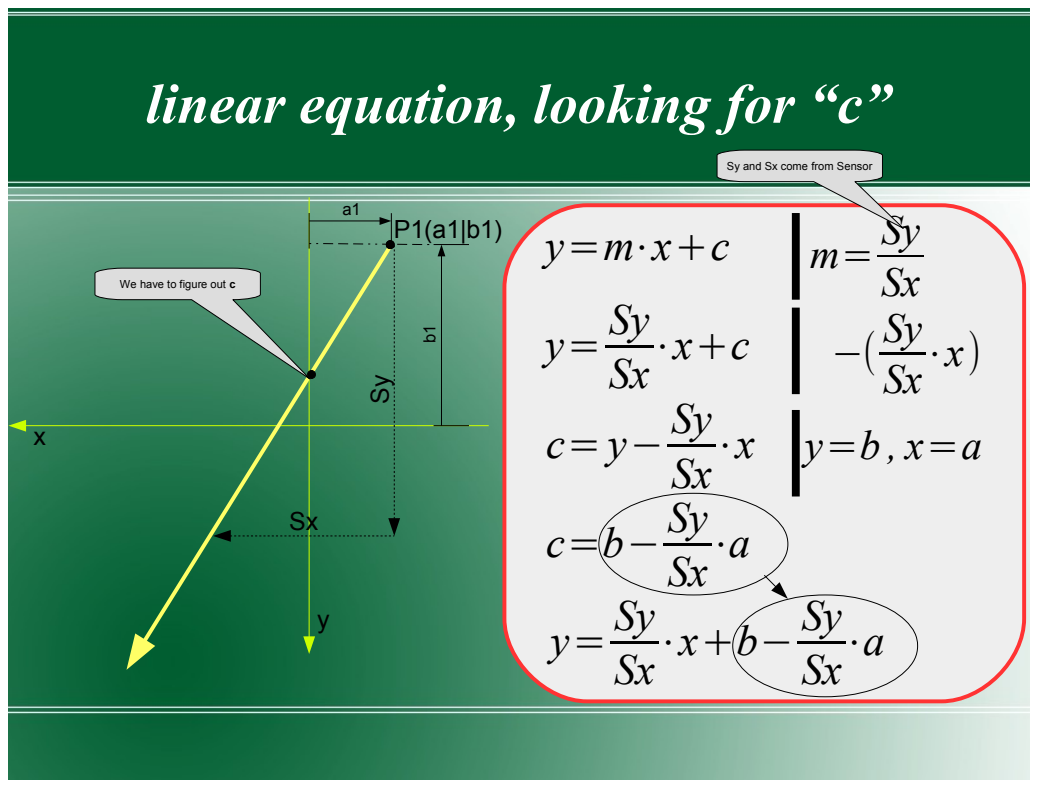
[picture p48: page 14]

Sy and Sx come from Sensor

We have to figure out c

# Intersection of two lines in general 1/4

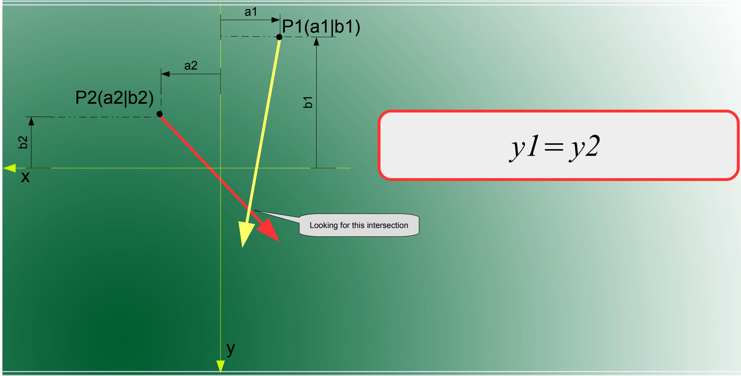
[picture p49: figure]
Looking for this intersection

# Intersection of two lines in general 2/4

y1=y2

## S y₁ S x₁

## ⋅x+b₁−

## S y₁ S x₁

⋅a₁=

## S y₂ S x₂

## ⋅x+b₂−

## S y₂ S x₂

### ⋅a₂ −(b₁−

## S y₁ S x₁

⋅a₁)

## S y₁ S x₁

⋅x=

## S y₂ S x₂

## ⋅x+b₂−

## S y₂ S x₂

## ⋅a₂−(b₁−

## S y₁ S x₁

⋅a₁) −(

## S y₂ S x₂

⋅x)

## S y₁ S x₁

⋅x−

## S y₂ S x₂

## ⋅x=b₂−

## S y₂ S x₂

## ⋅a₂−(b₁−

## S y₁ S x₁

⋅a₁)

# Intersection of two lines in general 3/4

x⋅(

## S y₁ S x₁

−

## S y₂ S x₂

)=b₂−

## S y₂ S x₂

## ⋅a₂−(b₁−

## S y₁ S x₁

< | ⋅a₁) | :(

## S y₁ S x₁

−

## S y₂ S x₂

)

x=

b₂−

## S y₂ ⋅a₂ S x₂

−(b₁−

## S y₁ ⋅a₁ S x₁

)

(

## S y₁ S x₁

−

## S y₂ S x₂

)

<

# Intersection of two lines in general 4/4

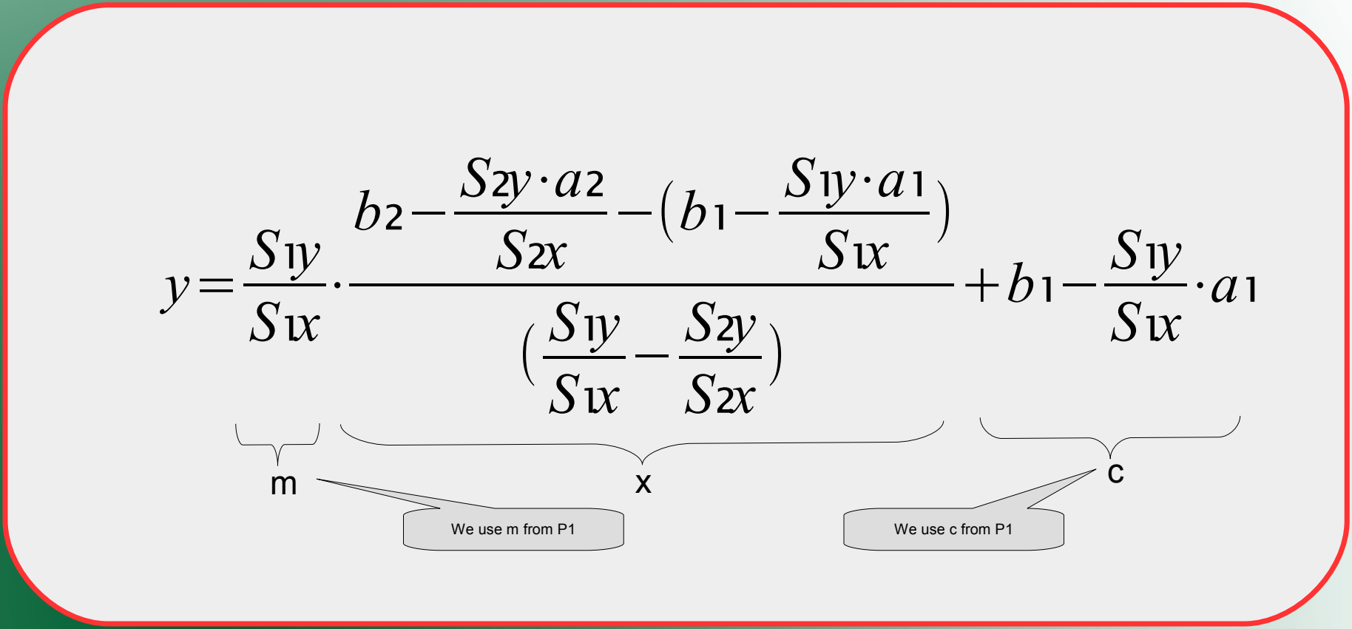
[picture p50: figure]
We use m from P1; We use c from P1

# Division by zero 1/3

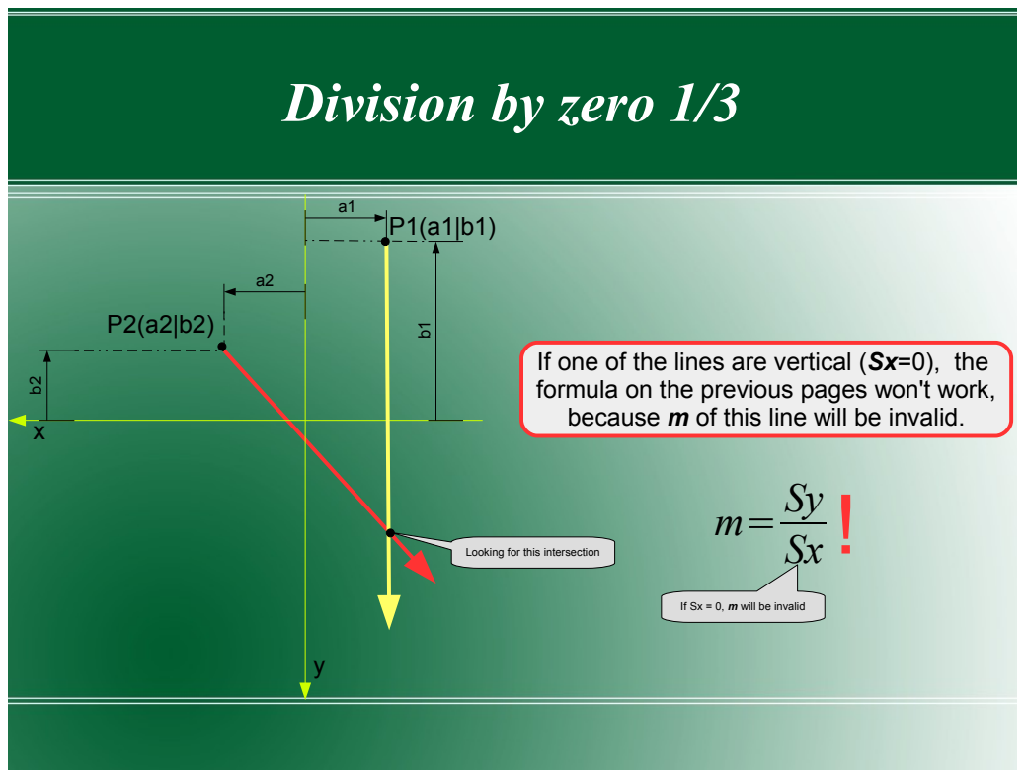
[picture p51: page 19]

If one of the lines are vertical (Sx=0), the
formula on the previous pages won't work,
because m of this line will be invalid.

Looking for this intersection

If Sx = 0, m will be invalid

# Division by zero 2/3

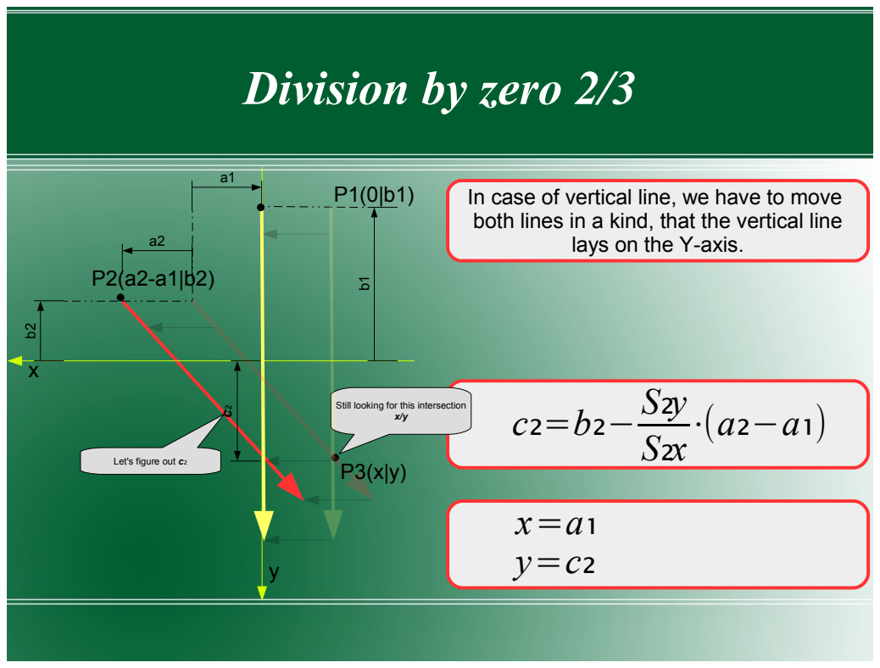
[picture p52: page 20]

In case of vertical line, we have to move
both lines in a kind, that the vertical line

lays on the Y-axis.

Still looking for this intersection

Let's figure out c₂

# Division by zero 3/3

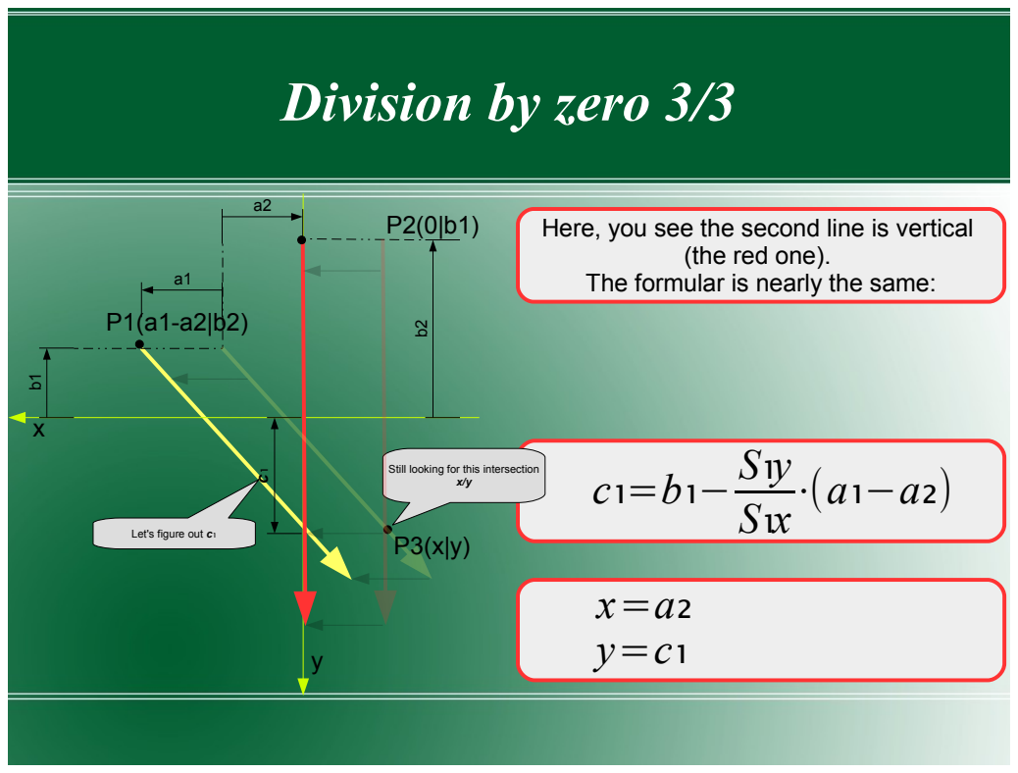
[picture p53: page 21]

Here, you see the second line is vertical

(the red one).

The formular is nearly the same:

Still looking for this intersection

Let's figure out c₁

# Center of the foot

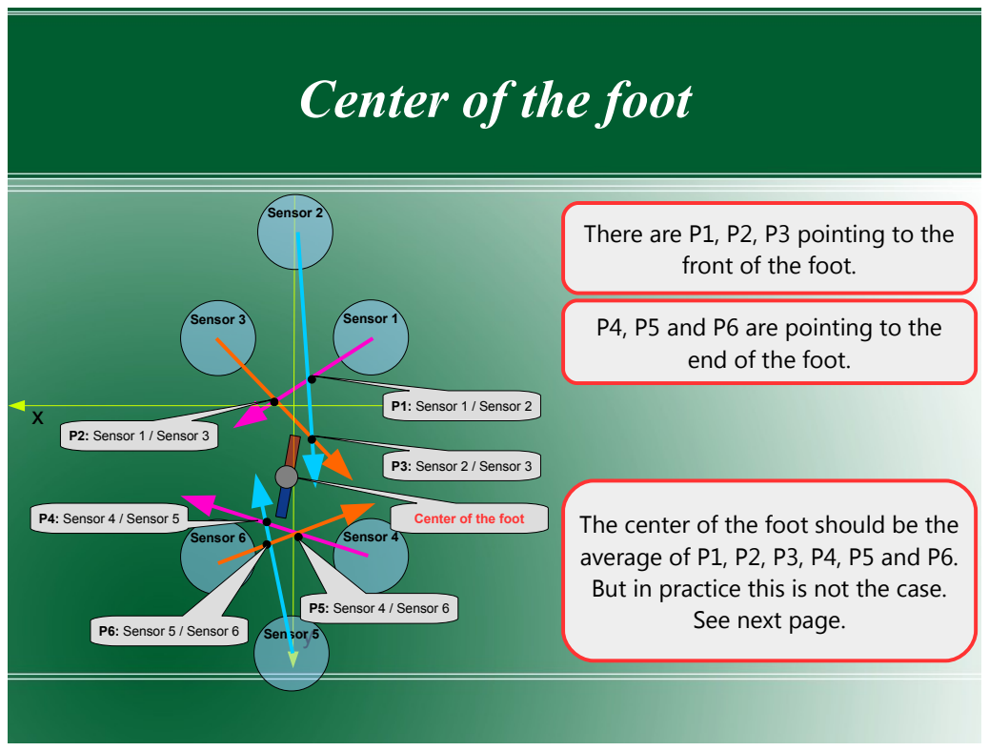
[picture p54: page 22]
Sensor 3; Sensor 1; P1: Sensor 1 / Sensor 2; Sensor 2; P3: Sensor 2 / Sensor 3; P2: Sensor 1 / Sensor 3; Sensor 6; Sensor 4; Sensor 5; P4: Sensor 4 / Sensor 5; P5: Sensor 4 / Sensor 6; P6: Sensor 5 / Sensor 6

There are P1, P2, P3 pointing to the

front of the foot.

P4, P5 and P6 are pointing to the
end of the foot.

Center of the foot

The center of the foot should be the
average of P1, P2, P3, P4, P5 and P6.
But in practice this is not the case.

See next page.

# Magnetic field lines/too close to sensor

When the magnet is too close to the magnetic field sensor, this sensor will produce useless data, because of the magnet field lines, coming “out” of the magnet.

The tangent of the field lines then changes very quickly and point to the “wrong” direction.

But the good thing: if the magnet is too close to one of the magnet field sensors, the distance to the other two magnetic field sensors is increased. So, we have to trust the other two magnetic field sensor datas and to ignore the third one which create useless data.

Center of the sensor
The tangent of this fieldline is causing wrong values.

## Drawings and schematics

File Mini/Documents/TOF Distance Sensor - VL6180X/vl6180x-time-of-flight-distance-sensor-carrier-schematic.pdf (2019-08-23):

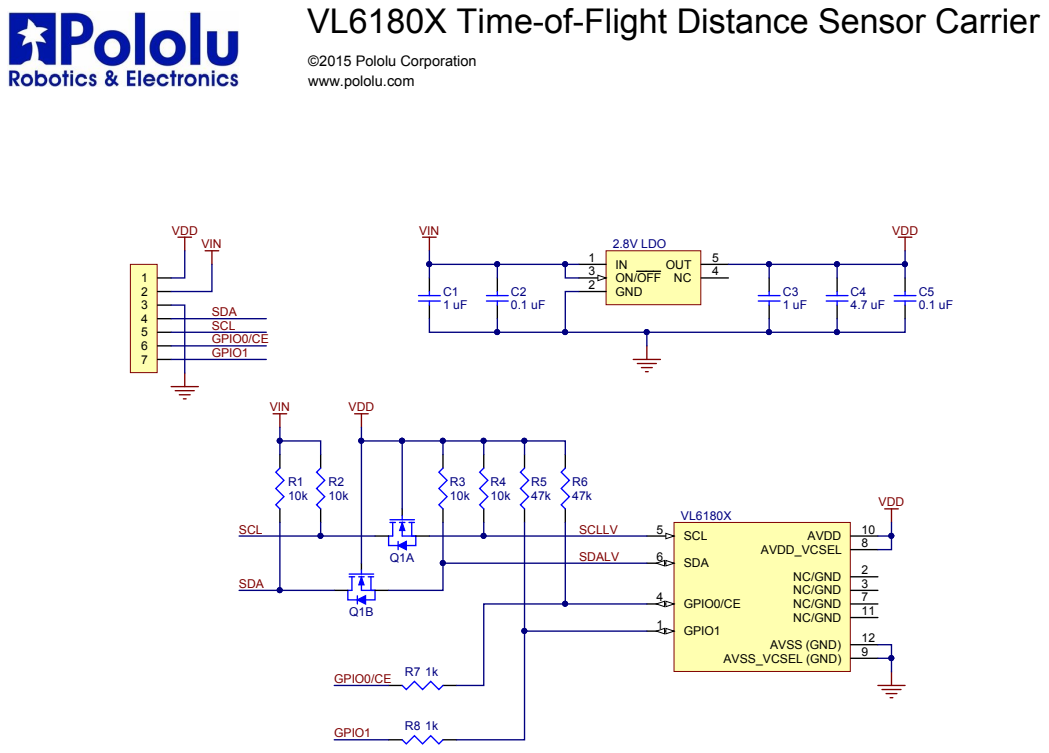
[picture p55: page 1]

VL6180X Time-of-Flight Distance Sensor Carrier

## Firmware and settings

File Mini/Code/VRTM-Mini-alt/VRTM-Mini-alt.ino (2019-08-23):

#include <avrlibdefs.h>
#include <nI2C.h>
#include <nTWI.h>
#include <queue.h>
#include <Servo.h>

/* ****************************************** D I V E R S E - K O N S T A N T E N *******************************************
   
  ************************************************************************************************************************** */
typedef struct
{
  bool PIN_STEPPER_COIL1_PLUS;
  bool PIN_STEPPER_COIL2_PLUS;
  bool PIN_STEPPER_COIL1_MINUS;
  bool PIN_STEPPER_COIL2_MINUS;
} tStepperPins;
/*
//                                          PIN_STEPPER_COIL1_PLUS, PIN_STEPPER_COIL2_PLUS, PIN_STEPPER_COIL1_MINUS,  PIN_STEPPER_COIL2_MINUS
const tStepperPins HorizontalAxisSteps[] = {{LOW,                   LOW,                    LOW,                      HIGH},
                                            {LOW,                   LOW,                    HIGH,                     LOW},
                                            {LOW,                   HIGH,                   LOW,                      LOW},
                                            {HIGH,                  LOW,                    LOW,                      LOW}};
*/                                    
//                                          PIN_STEPPER_COIL1_PLUS, PIN_STEPPER_COIL2_PLUS, PIN_STEPPER_COIL1_MINUS,  PIN_STEPPER_COIL2_MINUS
const tStepperPins HorizontalAxisSteps[] = {{HIGH,                  LOW,                    LOW,                      LOW},
                                            {LOW,                   HIGH,                   LOW,                      LOW},
                                            {LOW,                   LOW,                    HIGH,                     LOW},
                                            {LOW,                   LOW,                    LOW,                      HIGH}};

// Position of the GY271 sensors on each footplate:
const double GY271_Sensor_X[] = {         -(40.64/2),          0.0,          (40.64/2),        -(40.64/2),          0.0,         (40.64/2) };
const double GY271_Sensor_Y[] = { -(143.149/2)+21.23, -(143.149/2), -(143.149/2)+21.23, (143.149/2)-22.86,  (143.149/2), (143.149/2)-22.86 };

const char MOTOR_BREAK_SPEED         = 110;
const char MOTOR_LOW_SPEED           = 0;
const char MOTOR_HIGH_SPEED          = 80;             // Der Motor darf maximal 6V erhalten
                                                       // Es liegen am Motortreiber "L298N" 12V extern an. Er besitzt 1,4V Verlust
                                                       // D.h. ein 
                                                       // PWM mit   0 = 0V
                                                       // PWM mit 144 = 5,986V
                                                       // PWM mit 255 = 10,6V (12V - 1,4 Verlust)

/* ********************************************** P I N - A S S I G N M E N T ***********************************************
   ************************************************************************************************************************** */
const char PIN_USB_RX                = 0;   // USB BUS RX
const char PIN_USB_TX                = 1;   // USB BUS TX
const char PIN_BASEPLATE_ENCODER_A   = 2;   // INT     Plattform Encoder: INT Input
const char PIN_BASEPLATE_ENCODER_B   = 3;   // PWM,INT Plattform Encoder: INT Input
const char PIN_STEPPER_COIL2_PLUS    = 4;   //         Stepper Driver for wire pair: Green/Black (IN2), The stepper is always enabled
const char PIN_RESERVE_1             = 5;   // PWM
const char PIN_BASEPLATE_MOTOR_ENABLE= 6;   // PWM     Plattform Motor: PWM Signal für Geschwindigkeit (Achtung: der Motor verträgt 6V)
const char PIN_BASEPLATE_MOTOR1_PLUS = 7;   //         Plattform Motor: Richtung Plus/Clockwise
const char PIN_BASEPLATE_MOTOR1_MINUS= 8;   //         Plattform Motor: Richtung Minus/Counter clockwise
const char PIN_FOOTPRINT_RIGHT_SERVO = 9;   // PWM     Trittplatte links: Servo position links, 1ms..2ms=-90°..+90°
const char PIN_FOOTPRINT_LEFT_SERVO  = 10;  // PWM     Trittplatte rechts: Servo position rechts, 1ms..2ms=-90°..+90°
const char PIN_RESERVE_2             = 11;  // PWM
const char PIN_STEPPER_COIL1_PLUS    = 12;  //         Stepper Driver for wire pair: red/blue (IN4), The stepper is always enabled
const char PIN_STEPPER_COIL1_MINUS   = 13;  //         Stepper Driver for wire pair: red/blue (IN3), The stepper is always enabled
const char PIN_REFERENCE_SWITCH      = A0;  // A0      
const char PIN_STEPPER_COIL2_MINUS   = A1;  // A1      Stepper Driver for wire pair: Green/Black (IN1), The stepper is always enabled
const char PIN_BASEPLATE_MOTOR2_PLUS = A2;  // A2
const char PIN_BASEPLATE_MOTOR2_MINUS= A3;  // A3
const char PIN_I2C_BUS_SDA           = A4;  // A4      I2C BUS: SDA
const char PIN_I2C_BUS_SCL           = A5;  // A5      I2C BUS: SCL

/* ****************************************************** T Y P E S *********************************************************
   ************************************************************************************************************************** */
typedef struct {
  double X;
  double Y;
} tPosition;

typedef struct {
  int X;
  int Y;
  int Z;
} tGY271_Offset;

typedef struct {
  boolean SetOffset;
  tGY271_Offset Value;
  tGY271_Offset Offset;
  bool Valid;
  bool Started;
} tGY271;

typedef struct {
  byte Range;
  byte Status;
} tVL6180X;

typedef struct {
  int CurrentPosition;
  int DestinationPosition;  
} tStepper;

/* tFootprint
   ~~~~~~~~~~
   Diese Struktur enthält alle Parameter einer Trittplatte.
   Siehe Dokument "VRTM - Crosswalk - Formeln um einen Fuß zu folgen"
*/
typedef struct {
  long fx;                  // X Position der Trittplatte im Raum
  long fy;                  // Y Position der Trittplatte im Raum
  long b;                   // gewünschter Abstand der Trittplatte zum Drehzentrum
  float deltaAlpha;         // gewünschter Delta-Dreh-Winkel der Plattform
  float alpha;              // gewünschter Dreh-Winkel der Plattform
  float deltaBeta;          // gewünschter Delta-Dreh-Winkel der Plattform
  int   ServoMicroseconds;  // gewünschter Dreh-Winkel der Trittplattform in Servo-gerechter Zahl (1000 ... 2000 = -90° ... +90°) 
  float beta;               // gewünschter Dreh-Winkel der Trittplattform
  Servo sServo;             // Ist der Motor, der die Trittplatte dreht
  tGY271 GY271[6];          // Sensorvalues from all of the GY271 sensors
  tVL6180X VL6180X[6];      // Sensorvalues from all of the VL6180X sensors
  tPosition Center;         // The current center of the foot above the footplate
  bool CenterValid;
  CI2C::Handle I2C_TCA9548A_Upper;
  CI2C::Handle I2C_TCA9548A_Lower;
} tFootprint;

/* tBasePlate
   Diese Struktur enthält alle Parameter die für die Plattform
   notwendig sind.
 */
typedef struct {
  volatile int iCurrentPosition;      // aktueller Pulszähler der Plattform. Eine Umdrehung sind 600x4 = 2400 Pulse. Gezählt wird von 0...1199 Pulse. Das entspricht 0..359 Grad
  volatile char cCurrentState;        // aktueller "State" von PIN A und PIN B des Encoders. Wird f�r den Interrupt benötigt
  volatile int iDestinationPosition;  // Zielposition der Plattform. Die Motoren werden die Plattform in Position bringen.
  volatile int iPreviousDestinationPosition;
  volatile tStepper HorizontalAxis;
  volatile long lCurrentSpeed;
  volatile long lPreviousSpeed;
  volatile byte bMoving;
} tBasePlate;

/* *********************************************  G L O B A L    V A R I A B L E S ******************************************
   ************************************************************************************************************************** */
volatile byte PID_KI=0;

volatile byte bPWM;
byte bPreviousPWM;
long lPreviousSpeed;
byte HorizontalAxisIndex;
byte bSTOP_CurrentTCA9548A;
byte bSTOP_CurrentTCA9548A_Port;

// I2C Send and receive buffer:
byte    cGY271_ReceiveBuffer[10]={0};
byte    cTCA9548A_SendBuffer[]={0,1,2,4,8,16,32,64,128};
byte    cZero[1]={0};
byte bInterrupt;
tGY271 *pGY271_Callback_Sensor;

tBasePlate BasePlate;
tFootprint FootprintLeft;
tFootprint FootprintRight;
double fDistanceFactor;
CI2C::Handle I2C_GY271;
CI2C::Handle I2C_VL6180X;

unsigned long ulStart;
unsigned long ulStop;
unsigned long ulCycles;
/* ***************************************************  B A S E P L A T E  **************************************************
   ************************************************************************************************************************** 
   Dieser Abschnitt enthält alle Funktionen für die sich drehende Plattform.
   Auch mit dabei ist die Ansteuerung der Motoren um die Plattform zu drehen.
   Damit sich die Plattform dreht, und die Motoren angesteuert werden, ist zunächst
   die Funktion "fBasePlate_Init" aufzurufen. Anschließend ist lediglich
   die folgende Variable auf die anzufahrende Zielposition zu setzen:

   BasePlate.iDestinationPosition = 0..1199, wobei dies 0..359° entspricht

   Soll die Plattform langsam anfahren und auch bremsen kurz vor der Zielposition,
   so ist diese Variable zu setzen: ACC_BASEPLASTE_DISTANCE

   Wenn die zu fahrende Strecke der Plattform kleiner ist als die Anzahl der Pulse (0..1199)
   in ACC_BASEPLASTE_DISTANCE, so werden die Motoren per PWM langsam gestartet bzw. abgebremst.

   Ist die zurück zu legende Strecke größer als ACC_BASEPLASTE_DISTANCE, so wird gleich
   von Begin an die Motoren zu 100% angesteuert.

   Ist kein Abbremsen oder langsames Beschleunigen gewünscht, so ist die Konstante
   ACC_BASEPLASTE_DISTANCE auf 0 zu setzen.
  
 */

/* Function: fBasePlate_Move
   Description:
    Diese Funktion dreht die eigentliche Plattform. Sie wird von 
    der Interrupt Funktion fBasePlate_Interrupt aufgerufen.
    Die Motoren werden so angesteuert, dass die gewünschte 
    Zielposition "iDestinationPosition" automatisch angefahren wird.
    Diese Funktion wird vom Interrupt des Encoders automatisch 
    aufgerufen. Siehe Funktion: "fBasePlate_Interrupt"
    Es ist also nicht notwendig, diese Funktion manuell/direkt 
    aufzurufen.

   PARAMETERS:  none
   USES:        BasePlate.iDestinationPosition
                BasePlate.iCurrentPosition
   MODIFYS:     PIN_BASEPLATE_MOTOR_MINUS
                PIN_BASEPLATE_MOTOR_PLUS
   DURATION:    ?
   USED BY:     fBasePlate_Interrupt     
   
 */

void fBasePlate_Move () {
  int iDeltaMinus;
  int iDeltaPlus;
  if ((BasePlate.iDestinationPosition!=BasePlate.iCurrentPosition) && (BasePlate.iPreviousDestinationPosition!=BasePlate.iDestinationPosition)) { 
    // die Achse muss sich in Bewegung setzen
    // Zunächst ermitteln, ob sich diese links oder rechtsherum drehen muss.
    // Problem: es gibt einen Überlauf von 1199 auf 0 und umgekehrt.
    if (BasePlate.iDestinationPosition > BasePlate.iCurrentPosition) { 
      iDeltaPlus = BasePlate.iDestinationPosition - BasePlate.iCurrentPosition;
      iDeltaMinus = BasePlate.iCurrentPosition + (1199 - BasePlate.iDestinationPosition);
    }
    else {
      iDeltaMinus = BasePlate.iCurrentPosition - BasePlate.iDestinationPosition;
      iDeltaPlus = BasePlate.iDestinationPosition + (1199 - BasePlate.iCurrentPosition);
    }
    if (iDeltaPlus<iDeltaMinus) { 
      // die Plattform muss sich rechts-herum drehen
      bPWM=PID_KI;
      digitalWrite (PIN_BASEPLATE_MOTOR1_MINUS, LOW);
      digitalWrite (PIN_BASEPLATE_MOTOR1_PLUS, HIGH);
      digitalWrite (PIN_BASEPLATE_MOTOR2_MINUS, LOW);
      digitalWrite (PIN_BASEPLATE_MOTOR2_PLUS, HIGH);
      analogWrite (PIN_BASEPLATE_MOTOR_ENABLE, bPWM);
      BasePlate.bMoving=1;
      return;
    }
    else 
    if (iDeltaMinus<iDeltaPlus) {
      // die Plattform muss sich links-herum drehen
      bPWM=PID_KI;
      digitalWrite (PIN_BASEPLATE_MOTOR1_PLUS, LOW);
      digitalWrite (PIN_BASEPLATE_MOTOR1_MINUS, HIGH);
      digitalWrite (PIN_BASEPLATE_MOTOR2_PLUS, LOW);
      digitalWrite (PIN_BASEPLATE_MOTOR2_MINUS, HIGH);
      analogWrite (PIN_BASEPLATE_MOTOR_ENABLE, bPWM);
      BasePlate.bMoving=1;
      return;
    }
  }
  // Plattform ist bereits in Position, also die Bremse betätigen:
  BasePlate.bMoving=0;
  BasePlate.iPreviousDestinationPosition = BasePlate.iDestinationPosition;
  digitalWrite (PIN_BASEPLATE_MOTOR1_MINUS, HIGH);
  digitalWrite (PIN_BASEPLATE_MOTOR1_PLUS, HIGH);
  digitalWrite (PIN_BASEPLATE_MOTOR2_MINUS, HIGH);
  digitalWrite (PIN_BASEPLATE_MOTOR2_PLUS, HIGH);
  analogWrite (PIN_BASEPLATE_MOTOR_ENABLE, MOTOR_BREAK_SPEED);      
}


/* Function: fBasePlate_GetCurrentState
   Description:
     Diese Funktion ermittelt den aktuellen Zustand (1..4) der Plattform
     bzw. in welcher der vier Stati sich die Plattform befindet.
     Wird später der vorherige "State" mit dem aktuellen "State"
     verglichen, kann die Drehrichtung der Plattform ermittelt werden.
     
   PARAMETERS:  none
   USES:        PIN_BASEPLATE_ENCODER_A
                PIN_BASEPLATE_ENCODER_B
   MODIFYS:     BasePlate.cCurrentState
   DURATION:    ?
   USED BY:     fBasePlate_Interrupt
                fBasePlate_Init
 
 */
void fBasePlate_GetCurrentState () {
  bool Channel_A;
  bool Channel_B;
  Channel_A = digitalRead (PIN_BASEPLATE_ENCODER_A);
  Channel_B = digitalRead (PIN_BASEPLATE_ENCODER_B);
  if (Channel_A == HIGH) {
    if (Channel_B == LOW)
      BasePlate.cCurrentState = 1;  // State=1: PINA = 1, PINB = 0
    else
      BasePlate.cCurrentState = 2;  // State=2: PINA = 1, PINB = 1
  }
  else { // Channel_A==LOW
    if (Channel_B == HIGH)
      BasePlate.cCurrentState = 3;  // State=3: PINA = 0, PINB = 1
    else
      BasePlate.cCurrentState = 4;  // State=4: PINA = 0, PINB = 0
  }  
}

/* Function: fBasePlate_Interrupt
   Description:
    Wird vom Encoder aufgerufen wenn sich dieser dreht.
    Daraus wird die aktuelle IST Position der Platforrm
    ermittelt.
    Es ändert sich entweder der Zustand von PIN A oder B.
    Sobald sich die Spannung an einem der beiden PINs
    ändert, wird diese Funktion aufgerufen.
    Bei jeden Interrupts kann sich "State" wie folgt
    ändern:
      STATE: 1 2 3 4 1 2 3 4
      ======================
      PIN A: 1 1 0 0 1 1 0 0
      PIN B: 0 1 1 0 0 1 1 0
    Beispiel:
    Ist zum Zeitpunkt des Interrupts der PINA=1 und
    PINB=1, so handelt es sich um "State=2".
    Verglichen mit dem vorherigen State, kann
    ermittelt werden ob sich der Encoder links oder
    rechts herum dreht.
    Gezählt wird von 0..1199 was 0..359 Grad entspricht.
    Dieser Interrupt ruft auch die Funktion
    fBasePlate_MotorMove auf, um sofort die 
    Motoren entsprechend zu korrigieren.
   
   PARAMETERS:  none
   USES:        BasePlate.cCurrentState
                fBasePlate_Move
                fBasePlate_GetCurrentState
   MODIFYS:     BasePlate.iCurrentPosition
   DURATION:    ?
   USED BY:     PIN_BASEPLATE_ENCODER_A
                PIN_BASEPLATE_ENCODER_B
*/
void fBasePlate_Interrupt () {
  char cPreviousState;
  
  BasePlate.lCurrentSpeed++;
  
  cPreviousState = BasePlate.cCurrentState;
  fBasePlate_GetCurrentState ();
  if (cPreviousState < BasePlate.cCurrentState) {
    // Encoder dreht sich links herum
    if (BasePlate.iCurrentPosition > 0)
      BasePlate.iCurrentPosition--;         // Encoder dreht sich links
    else
      BasePlate.iCurrentPosition = 1199;    // Überlauf, zurück zu 1199 da es in den Minusbereich nicht gehen darf
  }
  else { 
    // Encoder dreht sich (hoffentlich) rechts herum
    if (BasePlate.iCurrentPosition < 1199)
      BasePlate.iCurrentPosition++;         // Encoder dreht sich rechts
    else
      BasePlate.iCurrentPosition = 0;       // Überlauf, zurück zu 0, da hier nicht höher als 1199 gezählt werden darf
  }
  fBasePlate_Move ();                       // die Motoren ansteuern
}
 
/* Function: fBasePlate_Init
   Description:
    Diese Funktion ist aufzurufen damit der Encoder initialisiert wird.
    Hier werden die PINs als Eingang deklariert, der aktuelle "State"
    des Encoders ermittelt als auch die Interrupts des Encoders aktiviert.

   PARAMETERS:  none
   USES:        PIN_BASEPLATE_ENCODER_A
                PIN_BASEPLATE_ENCODER_B
                fBasePlate_GetCurrentState
   MODIFYS:     PIN_BASEPLATE_ENCODER_A
                PIN_BASEPLATE_ENCODER_B
                PIN_BASEPLATE_MOTOR_PLUS
                PIN_BASEPLATE_MOTOR_MINUS
                BasePlate.iCurrentPosition
                BasePlate.iDestinationPosition
   DURATION:    ?
   USED BY:     setup
*/
void fBasePlate_Init () {
  Serial.println ("fBasePlate_Init");
  pinMode (PIN_BASEPLATE_ENCODER_A, INPUT_PULLUP);
  pinMode (PIN_BASEPLATE_ENCODER_B, INPUT_PULLUP);
  pinMode (PIN_BASEPLATE_MOTOR1_PLUS, OUTPUT);
  pinMode (PIN_BASEPLATE_MOTOR1_MINUS, OUTPUT);
  pinMode (PIN_BASEPLATE_MOTOR2_PLUS, OUTPUT);
  pinMode (PIN_BASEPLATE_MOTOR2_MINUS, OUTPUT);
  pinMode (PIN_BASEPLATE_MOTOR_ENABLE, OUTPUT);
  pinMode (PIN_REFERENCE_SWITCH, INPUT_PULLUP);
  digitalWrite (PIN_BASEPLATE_MOTOR1_PLUS, LOW);
  digitalWrite (PIN_BASEPLATE_MOTOR1_MINUS, LOW);
  digitalWrite (PIN_BASEPLATE_MOTOR2_PLUS, LOW);
  digitalWrite (PIN_BASEPLATE_MOTOR2_MINUS, LOW);
  digitalWrite (PIN_BASEPLATE_MOTOR_ENABLE, LOW);
  analogWrite (PIN_BASEPLATE_MOTOR_ENABLE, 0);
  pinMode (PIN_STEPPER_COIL1_PLUS, OUTPUT);
  pinMode (PIN_STEPPER_COIL1_MINUS, OUTPUT);
  pinMode (PIN_STEPPER_COIL2_PLUS, OUTPUT);
  pinMode (PIN_STEPPER_COIL2_MINUS, OUTPUT);
  digitalWrite (PIN_STEPPER_COIL1_PLUS,LOW);
  digitalWrite (PIN_STEPPER_COIL1_MINUS,LOW);
  digitalWrite (PIN_STEPPER_COIL2_PLUS,LOW);
  digitalWrite (PIN_STEPPER_COIL2_MINUS,LOW);
  fBasePlate_GetCurrentState ();
  BasePlate.HorizontalAxis.CurrentPosition=600;
  BasePlate.iCurrentPosition = 600;
  BasePlate.iDestinationPosition = 600;
  attachInterrupt (digitalPinToInterrupt(PIN_BASEPLATE_ENCODER_A), fBasePlate_Interrupt, CHANGE);
  attachInterrupt (digitalPinToInterrupt(PIN_BASEPLATE_ENCODER_B), fBasePlate_Interrupt, CHANGE);
}

/* ***************************************************  F O O T P R I N T *************************************************** 
   **************************************************************************************************************************
   Dieser Abschnitt enthält alle Funktionen die zur Ansteuerung einer Trittplatte notwendig sind.
 */


boolean fVL6180X_Synchron_ReadRegister8  (unsigned int uiRegister, byte *bValue) {
/*
  Wire.beginTransmission (0x29);
  Wire.write (uiRegister>>8);
  Wire.write (uiRegister);
  if (fI2C_CheckForError(Wire.endTransmission ())==false) 
  {
    Serial.print ("fVL6180X_Synchron_ReadRegister8, Wire.endTransmission failed: uiRegister=0x");
    Serial.println (uiRegister,HEX);
    fSTOP ();
    return false;
  }
  if (Wire.requestFrom (0x29,1)==1)
  {
    *bValue = Wire.read ();
    return true;
  }
  Serial.print ("fVL6180X_Synchron_ReadRegister8, Wire.endTransmission failed: uiRegister=0x");
  Serial.println (uiRegister,HEX);
  fSTOP ();
  */
  return false;
}

unsigned int fVL6180X_Synchron_ReadRegister16  (int bI2CAddress, unsigned int uiRegister) {
  unsigned int uiValue;
/*
  Wire.beginTransmission (bI2CAddress);
  Wire.write (uiRegister>>8);
  Wire.write (uiRegister);
  fI2C_CheckForError(Wire.endTransmission ());
  Wire.requestFrom (bI2CAddress,2);
  uiValue   = Wire.read ();
  uiValue <<= 8;
  uiValue  |= Wire.read();
  */
  return (uiValue);
}
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
void loop() {
  
  // Read values from Sensors:
  // ~~~~~~~~~~~~~~~~~~~~~~~~~
  //fGY271_Read_Values (); 

  //Serial.println (digitalRead (PIN_REFERENCE_SWITCH));
  //fSendDataToPC ();
  if (BasePlate.bMoving==0)
  {
    fBasePlate_Move ();  
  }
  fReceiveCommandsFromPC ();  
}

/* ***********************************************  I N T E R R U P T  ***********************************************
   ******************************************************************************************************************* */

// Interrupt is called every millisecond
ISR(TIMER0_COMPA_vect)  {  
  static int x;

  if (BasePlate.bMoving==1)
  {
    if (BasePlate.lCurrentSpeed<10)
    {
      if (PID_KI<MOTOR_HIGH_SPEED) PID_KI++;
    }
    if (BasePlate.lCurrentSpeed>20)
    {
      if (PID_KI>0) PID_KI--;
    }
    if (BasePlate.lCurrentSpeed!=0)
    {
      BasePlate.lPreviousSpeed=BasePlate.lCurrentSpeed;
    }
  }
  BasePlate.lCurrentSpeed=0;
  
  // STEPPER STUFF:
  // ~~~~~~~~~~~~~~
  if (digitalRead (PIN_REFERENCE_SWITCH)==HIGH) // Reference Switch active?
  { // Turn off motor
    digitalWrite (PIN_STEPPER_COIL1_PLUS,LOW);
    digitalWrite (PIN_STEPPER_COIL2_PLUS,LOW);
    digitalWrite (PIN_STEPPER_COIL1_MINUS,LOW);
    digitalWrite (PIN_STEPPER_COIL2_MINUS,LOW);
    BasePlate.HorizontalAxis.CurrentPosition=0;    
  }
  x++;
  if (x<8) return;
  x=0;
  if (BasePlate.HorizontalAxis.CurrentPosition!=BasePlate.HorizontalAxis.DestinationPosition)
  {
    if (BasePlate.HorizontalAxis.DestinationPosition>BasePlate.HorizontalAxis.CurrentPosition)
    {
      BasePlate.HorizontalAxis.CurrentPosition++;
      if (HorizontalAxisIndex<3)
      {
        HorizontalAxisIndex++;
      }
      else
      {
        HorizontalAxisIndex=0;
      }
    }
    else
    {
      BasePlate.HorizontalAxis.CurrentPosition--;
      if (HorizontalAxisIndex>0)
      {
        HorizontalAxisIndex--;
      }
      else
      {
        HorizontalAxisIndex=3;
      }
    }
    digitalWrite (PIN_STEPPER_COIL1_PLUS,HorizontalAxisSteps[HorizontalAxisIndex].PIN_STEPPER_COIL1_PLUS);
    digitalWrite (PIN_STEPPER_COIL2_PLUS,HorizontalAxisSteps[HorizontalAxisIndex].PIN_STEPPER_COIL2_PLUS);
    digitalWrite (PIN_STEPPER_COIL1_MINUS,HorizontalAxisSteps[HorizontalAxisIndex].PIN_STEPPER_COIL1_MINUS);
    digitalWrite (PIN_STEPPER_COIL2_MINUS,HorizontalAxisSteps[HorizontalAxisIndex].PIN_STEPPER_COIL2_MINUS);
  }
  else
  { // Turn off motor
    digitalWrite (PIN_STEPPER_COIL1_PLUS,LOW);
    digitalWrite (PIN_STEPPER_COIL2_PLUS,LOW);
    digitalWrite (PIN_STEPPER_COIL1_MINUS,LOW);
    digitalWrite (PIN_STEPPER_COIL2_MINUS,LOW);  
  }
}

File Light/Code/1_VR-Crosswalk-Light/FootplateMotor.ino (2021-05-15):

const char PIN_FOOTLEFT_ENCODER_A    = A0;  
const char PIN_FOOTLEFT_ENCODER_B    = A1;  
const char PIN_FOOTLEFT_PWM          =  9;  
const char PIN_FOOTLEFT_PLUS         =  7;
const char PIN_FOOTLEFT_MINUS        =  8;

const char PIN_FOOTRIGHT_ENCODER_A   = 4;  
const char PIN_FOOTRIGHT_ENCODER_B   = 5;  
const char PIN_FOOTRIGHT_PWM         = 6;  
const char PIN_FOOTRIGHT_PLUS        = A2;
const char PIN_FOOTRIGHT_MINUS       = A3;

const double ENCODER_PULSES_PER_360DEGREE = 3168; // Übersetzung des Getriebemotors ist 1:72, der Encoder hat 11 Pulse pro Motorumdrehung: 72 x 11 x 4 = 3168 Interrupts sind eine Umdrehung
static byte FootPower;

void pciSetup(byte pin)
{
    *digitalPinToPCMSK(pin) |= bit (digitalPinToPCMSKbit(pin));  // enable pin
    PCIFR  |= bit (digitalPinToPCICRbit(pin)); // clear any outstanding interrupt
    PCICR  |= bit (digitalPinToPCICRbit(pin)); // enable interrupt for the group
}

void FootplateMotor_setup ()
{
  FootPower=75;
  
  pinMode (PIN_FOOTLEFT_ENCODER_A, INPUT_PULLUP);
  pinMode (PIN_FOOTLEFT_ENCODER_B, INPUT_PULLUP);
  pinMode (PIN_FOOTLEFT_PWM, OUTPUT);
  analogWrite(PIN_FOOTLEFT_PWM,0);
  pinMode (PIN_FOOTLEFT_PLUS, OUTPUT);
  pinMode (PIN_FOOTLEFT_MINUS, OUTPUT);
  digitalWrite (PIN_FOOTLEFT_PLUS,LOW);
  digitalWrite (PIN_FOOTLEFT_MINUS,LOW);

  pinMode (PIN_FOOTRIGHT_ENCODER_A, INPUT_PULLUP);
  pinMode (PIN_FOOTRIGHT_ENCODER_B, INPUT_PULLUP);
  pinMode (PIN_FOOTRIGHT_PWM, OUTPUT);
  analogWrite(PIN_FOOTRIGHT_PWM,0);
  pinMode (PIN_FOOTRIGHT_PLUS, OUTPUT);
  pinMode (PIN_FOOTRIGHT_MINUS, OUTPUT);
  digitalWrite (PIN_FOOTRIGHT_PLUS,LOW);
  digitalWrite (PIN_FOOTRIGHT_MINUS,LOW);

  pciSetup (PIN_FOOTLEFT_ENCODER_A);
  pciSetup (PIN_FOOTLEFT_ENCODER_B);
  pciSetup (PIN_FOOTRIGHT_ENCODER_A);
  pciSetup (PIN_FOOTRIGHT_ENCODER_B);
  
  Footplate_Left.bEncoderPreviousChannelA = digitalRead (PIN_FOOTLEFT_ENCODER_A);
  Footplate_Left.bEncoderPreviousChannelB = digitalRead (PIN_FOOTLEFT_ENCODER_B);
  Footplate_Right.bEncoderPreviousChannelA = digitalRead (PIN_FOOTRIGHT_ENCODER_A);
  Footplate_Right.bEncoderPreviousChannelB = digitalRead (PIN_FOOTRIGHT_ENCODER_B);

  
}

ISR (PCINT0_vect) // handle pin change interrupt for D8 to D13 here
{
  //
}

ISR (PCINT1_vect) // handle pin change interrupt for A0 to A5 here
{ // Left footplate interrupt
  bool bEncoderChannelA;
  bool bEncoderChannelB;
  int bCurrentDirection;
  bEncoderChannelA = digitalRead (PIN_FOOTLEFT_ENCODER_A);    
  bEncoderChannelB = digitalRead (PIN_FOOTLEFT_ENCODER_B);
  if ((bEncoderChannelA==LOW)&&(bEncoderChannelB==HIGH))
  {
    if ((Footplate_Left.bEncoderPreviousChannelA==HIGH)&&(Footplate_Left.bEncoderPreviousChannelB==HIGH))
      bCurrentDirection=-1;
    else
      bCurrentDirection=1;
  }
  else
  if ((bEncoderChannelA==HIGH)&&(bEncoderChannelB==HIGH))
  {
    if ((Footplate_Left.bEncoderPreviousChannelA==LOW)&&(Footplate_Left.bEncoderPreviousChannelB==HIGH))
      bCurrentDirection=1;
    else
      bCurrentDirection=-1;
  }
  else
  if ((bEncoderChannelA==HIGH)&&(bEncoderChannelB==LOW))
  {
    if ((Footplate_Left.bEncoderPreviousChannelA==HIGH)&&(Footplate_Left.bEncoderPreviousChannelB==HIGH))
      bCurrentDirection=1;
    else
      bCurrentDirection=-1;
  }
  else
  if ((bEncoderChannelA==LOW)&&(bEncoderChannelB==LOW))
  {
    if ((Footplate_Left.bEncoderPreviousChannelA==HIGH)&&(Footplate_Left.bEncoderPreviousChannelB==LOW))
      bCurrentDirection=1;
    else
      bCurrentDirection=-1;
  }
  Footplate_Left.bEncoderPreviousChannelA=bEncoderChannelA;
  Footplate_Left.bEncoderPreviousChannelB=bEncoderChannelB;
  if (bCurrentDirection>0)
  {
    Footplate_Left.iEncoderPosition++;
  }
  else
  {
    Footplate_Left.iEncoderPosition--;
  }  
}  

ISR (PCINT2_vect) // handle pin change interrupt for D0 to D7 here
{ // Right footplate interrupt
  bool bEncoderChannelA;
  bool bEncoderChannelB;
  int bCurrentDirection;
  bEncoderChannelA = digitalRead (PIN_FOOTRIGHT_ENCODER_A);    
  bEncoderChannelB = digitalRead (PIN_FOOTRIGHT_ENCODER_B);
  if ((bEncoderChannelA==LOW)&&(bEncoderChannelB==HIGH))
  {
    if ((Footplate_Right.bEncoderPreviousChannelA==HIGH)&&(Footplate_Right.bEncoderPreviousChannelB==HIGH))
      bCurrentDirection=-1;
    else
      bCurrentDirection=1;
  }
  else
  if ((bEncoderChannelA==HIGH)&&(bEncoderChannelB==HIGH))
  {
    if ((Footplate_Right.bEncoderPreviousChannelA==LOW)&&(Footplate_Right.bEncoderPreviousChannelB==HIGH))
      bCurrentDirection=1;
    else
      bCurrentDirection=-1;
  }
  else
  if ((bEncoderChannelA==HIGH)&&(bEncoderChannelB==LOW))
  {
    if ((Footplate_Right.bEncoderPreviousChannelA==HIGH)&&(Footplate_Right.bEncoderPreviousChannelB==HIGH))
      bCurrentDirection=1;
    else
      bCurrentDirection=-1;
  }
  else
  if ((bEncoderChannelA==LOW)&&(bEncoderChannelB==LOW))
  {
    if ((Footplate_Right.bEncoderPreviousChannelA==HIGH)&&(Footplate_Right.bEncoderPreviousChannelB==LOW))
      bCurrentDirection=1;
    else
      bCurrentDirection=-1;
  }
  Footplate_Right.bEncoderPreviousChannelA=bEncoderChannelA;
  Footplate_Right.bEncoderPreviousChannelB=bEncoderChannelB;
  if (bCurrentDirection>0)
  {
    Footplate_Right.iEncoderPosition++;
  }
  else
  {
    Footplate_Right.iEncoderPosition--;
  }  
}
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

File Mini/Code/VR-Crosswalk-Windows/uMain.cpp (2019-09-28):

//---------------------------------------------------------------------------

#include <vcl.h>
#pragma hdrstop

#include "Math.h"
#include "uMain.h"
//---------------------------------------------------------------------------
#pragma package(smart_init)
#pragma link "PERFGRAP"
#pragma link "CSPIN"
#pragma resource "*.dfm"
TfrmMain *frmMain;

#define ScrollPoints 1
#define MaxPoints 500

//---------------------------------------------------------------------------
__fastcall TfrmMain::TfrmMain(TComponent* Owner)
        : TForm(Owner)
{
  hCom=INVALID_HANDLE_VALUE;
  bReceiveStarted=false;
  Dummy=0;
}
//---------------------------------------------------------------------------
void __fastcall TfrmMain::Close1Click(TObject *Sender)
{
  CloseComm (hCom);
  Close ();
}
//---------------------------------------------------------------------------
void __fastcall TfrmMain::COM11Click(TObject *Sender)
{
  if (OpenComm("COM1"))
  {
    COM11->Checked=true;
  }
}
//---------------------------------------------------------------------------
bool TfrmMain::OpenComm(char *Port)
{
  bReceiveStarted=false;
  CloseComm (hCom);
  hCom = ::CreateFile(Port,
                             GENERIC_READ | GENERIC_WRITE,
                             0,
                             0,
                             OPEN_EXISTING,
                             FILE_ATTRIBUTE_NORMAL,
                             0);

  if (hCom == INVALID_HANDLE_VALUE)
  {
    // ... Fehler
    MessageBox (0,"Com-Port not available","Error",0);
    return false;
  }
  iReceiveDataLength=0;
  SetDeviceControlBlock(hCom, 115000, 8, NOPARITY, ONESTOPBIT);
  return true;
}
//---------------------------------------------------------------------------
void TfrmMain::SetDeviceControlBlock(HANDLE hCom, DWORD BaudRate, BYTE ByteSize, BYTE Parity, BYTE StopBits)
{
  if (hCom == INVALID_HANDLE_VALUE) return;

  DCB dcb;

  // Schnittstelle auslesen
  if (!::GetCommState(hCom, &dcb))
  {
    // ... Fehler
  }

  dcb.BaudRate  = BaudRate;
  dcb.ByteSize  = ByteSize;
  dcb.Parity    = Parity;
  dcb.StopBits  = StopBits;

  // Schnittstelle konfigurieren
  if (!::SetCommState(hCom, &dcb))
  {
    // ... Fehler
  }

  COMMTIMEOUTS timeouts;

  timeouts.ReadIntervalTimeout = 1;
  timeouts.ReadTotalTimeoutMultiplier = 1;
  timeouts.ReadTotalTimeoutConstant = 1;
  timeouts.WriteTotalTimeoutMultiplier = 1;
  timeouts.WriteTotalTimeoutConstant = 1;
  SetCommTimeouts(hCom, &timeouts);

}
//---------------------------------------------------------------------------
int TfrmMain::SendData(HANDLE hCom, char *Data, int Length)
{
  DWORD NumberOfBytesWritten;
  if (hCom == INVALID_HANDLE_VALUE) return 0;
  if (!::WriteFile(hCom, Data, Length, &NumberOfBytesWritten, 0))
  {
    // ... Fehler
    NumberOfBytesWritten=0;
  }
  return NumberOfBytesWritten;
}
//---------------------------------------------------------------------------
DWORD TfrmMain::ReceiveData(HANDLE hCom, char *Data, int Length)
{
  DWORD NumberOfBytesRead;
  if (hCom == INVALID_HANDLE_VALUE) return 0;
  if (!::ReadFile(hCom, Data, Length, &NumberOfBytesRead, 0))
  {
    NumberOfBytesRead=0;// ... Fehler
  }
  return NumberOfBytesRead;
}
//---------------------------------------------------------------------------
void TfrmMain::CloseComm(HANDLE hCom)
{
  COM11->Checked=false;
  COM21->Checked=false;
  COM31->Checked=false;
  COM41->Checked=false;
  COM51->Checked=false;
  if (hCom == INVALID_HANDLE_VALUE) return;
  PurgeComm(hCom, PURGE_RXABORT);
  CloseHandle(hCom);
  hCom=INVALID_HANDLE_VALUE;
}
//---------------------------------------------------------------------------
void __fastcall TfrmMain::Timer1Timer(TObject *Sender)
{
  int iLength;
  char cData;
  if (hCom == INVALID_HANDLE_VALUE) return;
  Timer1->Enabled=false;
  for (int i=0;i<2048;i++)
  {
    iLength=ReceiveData(hCom,&cData,1);
    if (iLength==0) break;
    if ((cData!=13) && (cData!=10))
    {
      cReceiveData[iReceiveDataLength++]=cData;
    }
    if (cData=='\r')
    {
      cReceiveData[iReceiveDataLength]=0;
      iReceiveDataLength=0;
      // Daten sind vollständig übertragen
      fInterpreteReceivedData (cReceiveData);
      if (bUpdateChartMotor) UpdateChartMotor ();
      if (bUpdateChartStepper) UpdateChartStepper ();
    }
  }
  if (bRefreshDisplay==true)
  {
    bRefreshDisplay=false;
    DrawBaseplate(iMotor_EncoderPosition,iSteppermotor_CurrentPosition,
                iServoRightPosition,iServoLeftPosition,
                FootplateRight_SensorOffsetX,FootplateRight_SensorOffsetY,
                0,0);
  }
  Timer1->Enabled=true;
}
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

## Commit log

2019-06-29 Initial version of the baseplate
    [Baseplate-3mm.dxf, Baseplate-3mm.f3d]
2019-06-29 Initial version
    [Arduino Uno.f3d, PCB Spacer M3x5mm.f3d, Pulley, 16 tooths, drill hole 6mm.f3d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]
2019-06-29 wrong folder, so i delete it
    [Footplate.dxf, Footplate.fzz]
2019-06-29 restored because of wrong folder
    [Footplate.dxf, Footplate.fzz]
2019-07-17 Baseplate changed, ToDoList added, main wiring added
    [Arduino Shield.fzz, Baseplate-3mm.dxf, Baseplate-3mm.f3d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]
2019-07-18 Encoder and Footplate added
    [Encoder.f3d, Footplate.dxf, Footplate.f3d]
2019-08-06 Update 06.AUG.2019
    Programchange: I2C communication is now in parallel with main program.
    Wiring changed, because too much Ampere being used by the stepper motor.
    Document "Compass QMC5883" added, but still not finished, update needed.
    [Overview.fzz]
2019-08-23 Update 23.08.2019
    Still in development, most of the files will be changed, so don't take it Serious. It is just a backup of some of my files.
    [Overview.fzz]
2019-09-07 just a backup of some modified files, still not finished
    [Project1.obj, Unit1.obj]
2019-09-08 backup of 8 SEPT 2019
    New Windows GUI to communicate with the hardware
    [Project1.obj, Unit1.obj, VRCrosswalkMini.obj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]
2019-09-15 backup 15.09.2019
    [Project1.obj, Unit1.obj, uMain.obj]
2019-09-28 Backup 28.09.2019
    Stepper and Servo Control replaced by 3th Party library.
    Left footplate disables.
    [Project1.obj, Unit1.obj, uMain.obj]
2020-10-10 Create Bill of material.ods
    [Bill of material.ods]
2020-10-11 Update Bill of material.ods
    Itens 62..65 are new
    [Bill of material.ods]
2020-10-11 Update Bill of material.ods
    new items 66..68 added, also 8 more ISO 10642, M3x6mm added
    [Bill of material.ods]
2020-12-09 Update Bill of material.ods
    [Bill of material.ods]
2021-02-06 more files added
    [#5 Base plate, 5mm-1.dxf, Base.fzz]
2021-02-06 Wire diagram updated, and Excek added with Acceleration and so on added
    [Base.fzz, Wie verhalten sich die Achsen.xlsx]
2021-02-08 Wiring changed, Font size increased
    [Base.fzz]
2021-02-09 more documents
    [Slow walking velocity of an adult human.xlsx]
2021-02-13 Colors of wires updated, arduino code added (net yet finished)
2021-02-18 Update of 18 FEB 2021
    A lot of stuff has been changed, and there will be more changes in the future
    [Base.fzz]
2021-02-21 update 21.FEB.2021
    Now, the communication with all the I2C sensors is now working. But it is still in development.
